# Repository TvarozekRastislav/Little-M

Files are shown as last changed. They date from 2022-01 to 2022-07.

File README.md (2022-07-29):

# **Little M.**
<div style="text-align:center">
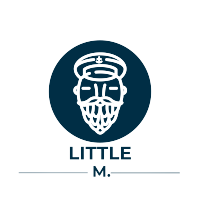
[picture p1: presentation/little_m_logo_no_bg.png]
    

Bechelors project of student at FEI STU Bratislava.<br> It is a prototype of little autonomous vehicle desinged to be able to orientate inside a building.<br>
Example video 1. - https://youtu.be/EsY_k1E6DLk<br>
Example video 2. - https://youtu.be/gij7saN3cls<br>
Bakalársky projekt študenta na FEI STU Bratislava.<br> Jedná sa o návrh malého autonómneho robotického vozdila s orientáciou v interieri.<br> Scrollni dole pre slovenský jazyk
</div>

---

## **Principle**
The basis of the project is the idea that there is already a wifi network almost everywhere around us. Using certain techniques, we can measure the Wi-Fi signal strength at a given location.
Determining which room the vehicle is in is based on collecting data on different signal strengths, different Wi-Fi networks (three in the project) and assigning the "id" of the room to these Wi-Fi networks. Subsequently, the data is processed and a model with an SVM calcifier is trained with them, so it is a so-called learning with a teacher. With the help of the openSource library, this model is subsequently converted into the C language so that it can be used in a vehicle that can use this model and the strength of the signal to find out which room it is in.

Project is composed from this parts
- ### data collector

- ### modeling part
- ### vehicle
---
### **data collector**
The purpose of this device is to measure signal strengths at the locations chosen by us.\
The preferred number is to perform 15 measurements in each room.\
The number of rooms is arbitrary.\
It consists of a USB Adapter for ESP-01, ESP8266 ESP-01 and a button that is used to access the programming mode.\
In the code, it is necessary to select the number of rooms, the number of Wi-Fi networks, their names, and how many measurements should be performed in each room.\
The code can be logged using putty or other software.\
When uploading the code, we will put the module into programming mode so that we hold the button while inserting it into the USB port.\
When programming, we must pay attention to the correct setting of the boaud height.\
**Parts**:
- Adapter for ESP-01
- ESP8266 ESP-01
- button

**schema**: 
- [schemas/zber_dat_png.png](https://github.com/TvarozekRastislav/Little-M./blob/main/schemas/zber_dat_png.png)

**code**:
- [code_base/data_collection.ino](https://github.com/TvarozekRastislav/Little-M./blob/main/code_base/data_collection/data_collection.ino)

**picture**:
- [hardware_pics/signal_collector.ino](https://github.com/TvarozekRastislav/Little-M./blob/main/hardware_pics/signal_collector.png)

---
### **Modeling part**

The task of the model part is to generate a "clean" csv file from the logged output from the previous part and use this file to train a model that uses the SVM classifier and then convert this model to a C file that can be used in Arduino using the open source micromlgen library.\
The model part can be done in two ways, by starting two jupyter notebooks or by setting the config and local execution of the script below or by pushing new input data.txt to the main branch, the GitHub action is started which generates the model and pushes it to GitHub.
With jupyternotebook, we can also see extra graphs related to data.

**schema**:
- [schemas/software_schema.png](https://github.com/TvarozekRastislav/Little-M./blob/main/schemas/software_schema.PNG)

**code**

***manual***:
- [code_base/data_clear_jupyter.ipynb](https://github.com/TvarozekRastislav/Little-M./blob/main/code_base/data_clear_jupyter.ipynb)
   - in the same folder, there must be an input file with data with the format from the previous section
   - the output is a csv file
- [code_base/data_train_model_jupyter.ipynb](https://github.com/TvarozekRastislav/Little-M./blob/main/code_base/data_train_model_jupyter.ipynb)
    - in the same folder, there must be an input file csv file with formatted data from the guessing point
    - the output is the model.h file which contains the trained model

***with help of script***:
- [code_base/create_model_automatic/config.json](https://github.com/TvarozekRastislav/Little-M./blob/main/code_base/create_model_automatic/config.json)
    - config needs to be changed to the required parameters
- [code_base/create_model_automatic/generate_model_from_data_file.py](https://github.com/TvarozekRastislav/Little-M./blob/main/code_base/create_model_automatic/generate_model_from_data_file.py)
    - to run the scirpt following requirements are required - [.github/workflows/requirements.txt](.github/workflows/requirements.txt)
---
### **Vehicle**
The vehicle uses an Arduino Uno and an Arduino sensor shield due to the large number of GND and VCC pins. The vehicle is powered by 4 motors that are controlled by H bridge modules, which allows you to set the speed of the vehicle as well as the direction of travel.\
  The Arduino is powered by two 4.5V batteries.
  It contains an ultrasonic sensor, a bluetooth receiver, ESP-01, a display that shows the current room in which the vehicle is located, 3 sensors for tracking a line on the ground.\
  The first code needs to be uploaded to the Arduino, the second to the ESP-01, then the vehicle can easily be controlled via a phone with a bluetooth connection, where the driving mode can be set, which will be line tracking or remote control.

 **schema**:
- [schemas/car_connected_pdf.png](https://github.com/TvarozekRastislav/Little-M./blob/main/schemas/car_connected_pdf.pdf)

**code**
- [code_base/car_code/main.ino](https://github.com/TvarozekRastislav/Little-M./blob/main/code_base/car_code/main/main.ino)
    - v rovnakom priečinku sa musí nachádzať aj model.h
    - tento kód je ptrebné nahrať na arduino
- [code_base/sending_via_rxtx](https://github.com/TvarozekRastislav/Little-M./blob/main/code_base/auto_wifi_signal_sender/sending_via_rxtx/sending_via_rxtx.ino)
    - tento kód je potrebné nahrať na ESp-01

**picture**:
- [hardware_pics/little_m_back.png](https://github.com/TvarozekRastislav/Little-M./blob/main/hardware_pics/little_m_back.png)

---

## **Princíp**
Základom projektu je myšlienka že takmer všade okolo nás sa už nachdáza wifi sieť. Pomocou určitých techník vieme zmerať silu wifi signálu na danom mieste.
Zisťovanie v akej miestnosti sa vozdilo nachádza je založené na zbere dát o rôznych silách signálov, rôznych wifi sietí(v projekte troch) a priradovania týmto wifi sietam aj "id" miestnosti. Následne sú dáta spracované a je nimi natrénovaný model s SVM kalsifikátorom teda ide o tzv. učenie s učiteľom. Pomocou openSource knižnice je následne tento model prevedený do jazyka C aby bol použiteľný vo vozidle ktoré vie pomocou tohoto modelu a sily signálu zistiť v akej miestnosti sa nachdáza.

Projekt je zložený z troch častí: 
- ### zariadenie na zber dát

- ### modelová časť
- ### vozidlo
---
### **Zariadenie na zber dát**
Toto zariadenie má za úlohu zmerať sily signálov na nami zvolených miestach.\
Preferovaný počet je v každej miestnosti vykonať 15 meraní.\
Počer miestností je ľubovoľný.\
Skladá sa z USB Adaptéra pre ESP-01, ESP8266 ESP-01 a tlačidla ktoré je používané na sprístupnenie programovancieho módu.\
V kóde je potrebné zvoliť počet miestností, počet wifi sietí, ich mená, a koľko meraní má byť v každej miestnosti vykonaných.\
Kód je možné loggovať pomocou putty alebo iného softwaru.\
Pri nahrávaní kódu uvedieme modul do programovacieho módu tak že pri vkladaní do USB portu budeme držať tlačidlo.\
Pri programovaní musíme dbať na správne nastavenie výšky boaudov.\
**súčiastky**:
- Adaptér pre ESP-01
- ESP8266 ESP-01
- tlačidlo

**schéma**: 
- [schemas/zber_dat_png.png](https://github.com/TvarozekRastislav/Little-M./blob/main/schemas/zber_dat_png.png)

**kód**:
- [code_base/data_collection.ino](https://github.com/TvarozekRastislav/Little-M./blob/main/code_base/data_collection/data_collection.ino)

**fotka**:
- [hardware_pics/signal_collector.ino](https://github.com/TvarozekRastislav/Little-M./blob/main/hardware_pics/signal_collector.png)

---
### **Modelová časť**

Modelová časť má za úlohu z loggovaného výstupu z predchádzajúcej časti vygenrovať "clean" csv súbor a pomocou tohoto súboru natrénovať model ktorý využíva SVM klasifikátor a následne tento model pomocou open source knižnice micromlgen prekonvertovať na súbor v jazyku C ktorý je možné využiť v arduine.\
Modelovú časť možno vykonať dvoma spôsobmi a to spustením dvoch jupyter notebookov alebo nastavením configu a lokálneho spustenia scriptu ktorý sa nachádza nižšie alebo pushnutím nových vstupných dát.txt do main branche sa spustá GitHub action  ktorá model vygeneruje a pushne na GitHub.
Pri jupyternotebooku môžeme vidieť aj extra grafy týkajúce sa dát.

**schéma**:
- [schemas/software_schema.png](https://github.com/TvarozekRastislav/Little-M./blob/main/schemas/software_schema.PNG)

**kód**

***manuálne***:
- [code_base/data_clear_jupyter.ipynb](https://github.com/TvarozekRastislav/Little-M./blob/main/code_base/data_clear_jupyter.ipynb)
    - v rovnakom priečinku sa musí nachádzať vstupný súbor s dátami s formátom z predchádzajúcej časti
    - vystupom je csv súbor 
- [code_base/data_train_model_jupyter.ipynb](https://github.com/TvarozekRastislav/Little-M./blob/main/code_base/data_train_model_jupyter.ipynb)
    - v rovnakom priečinku sa musí nachádzať vstupný súbor csv súbor s formátovanými dátami z predhádzajúceho bodu
    - výstupom je model.h súbor ktorý obsahuje natrénovaný model

***pomocou configu a scriptu***:
- [code_base/create_model_automatic/config.json](https://github.com/TvarozekRastislav/Little-M./blob/main/code_base/create_model_automatic/config.json)
    - config je potrebné zmeniť na požadované parametre
- [code_base/create_model_automatic/generate_model_from_data_file.py](https://github.com/TvarozekRastislav/Little-M./blob/main/code_base/create_model_automatic/generate_model_from_data_file.py)
    - na spustenie scriptu sú potrebné moduly ktoré sa nachádzajú v - [.github/workflows/requirements.txt](.github/workflows/requirements.txt)
---
### **Vozidlo**
Vozidlo využíva Arduino Uno a Arduino sensor shield kvoli veľkému množstvu GND a VCC pinov. Vozidlo je poháňané 4 motormi ktoré sú ovladané H bridge modulov, ktorý umožňuje nastavať rýchlosť vozidla ako aj smer jazdy.\
 Arduino je napájané dvomi 4.5V batériami.
 Obsahuje ultrazvukový senzor, bluetooth prijímač, ESP-01, display ktorý zobrazuje aktuálnu miestnosť v ktorej sa vozidlo nachádza, 3 senzori na sledovanie čiary na zemi.\
 Prvý kód je potrebné nahrať do Arduina druhý na ESP-01, potom je už jednoducho možné vozidlo ovládať cez telefón s bluetooth pripojením, kde sa dá nastavoať mód jazdy, a to bude sledovanie čiary alebo diaľkové ovládanie.

 **schéma**:
- [schemas/car_connected_pdf.png](https://github.com/TvarozekRastislav/Little-M./blob/main/schemas/car_connected_pdf.pdf)

**kód**
- [code_base/car_code/main.ino](https://github.com/TvarozekRastislav/Little-M./blob/main/code_base/car_code/main/main.ino)
    - v rovnakom priečinku sa musí nachádzať aj model.h
    - tento kód je ptrebné nahrať na arduino
- [code_base/sending_via_rxtx](https://github.com/TvarozekRastislav/Little-M./blob/main/code_base/auto_wifi_signal_sender/sending_via_rxtx/sending_via_rxtx.ino)
    - tento kód je potrebné nahrať na ESp-01

**fotka**:
- [hardware_pics/little_m_back.png](https://github.com/TvarozekRastislav/Little-M./blob/main/hardware_pics/little_m_back.png)

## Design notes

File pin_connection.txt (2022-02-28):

Servo - 9

H-bridge:
ENA - 3
ENB - 6
IN1 - 10
IN2 - 11
IN3 - 12
IN4 - 13 

Ultra Sensor:
trig - A1 
echo - A0

track-middle - 8
track-left - 7
track-right - 5

esp8266_module_rx - 2
esp8266_module_tx - 4

bluetooth_rx - tx 
bluetooth_tx - rx

Display: 
SDA - A4
SCL - A5

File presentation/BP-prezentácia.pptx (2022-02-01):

## AUTONÓMNE RIADENIE VOZIDLA V INTERIÉRI

Vedúci bakalárskej práce: Ing. Štefan (https://is.stuba.sk/auth/lide/clovek.pl)Bucz (https://is.stuba.sk/auth/lide/clovek.pl), PhD. (https://is.stuba.sk/auth/lide/clovek.pl)

Vypracoval: Rastislav Tvarožek

## OBSAH

1. Motivácia 2. Návrh riešenia 3. Hardware 4. Software 5. Plán na budúci semester

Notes: Abstrahovanie kvoli času

## MOTIVÁCIA

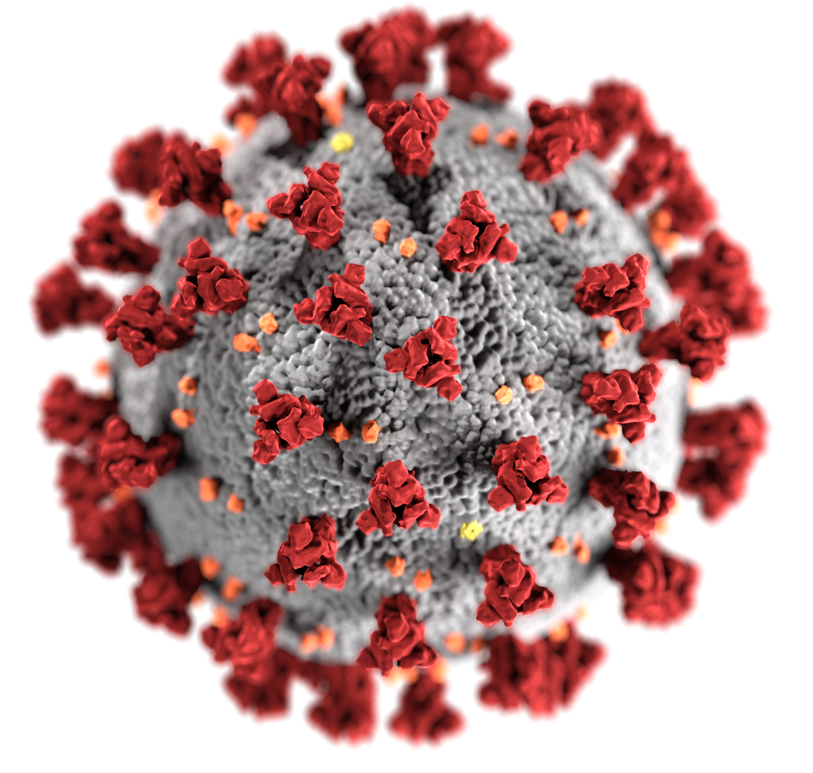
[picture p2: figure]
Obrázok, na ktorom je koláč, ozdobené, ovocie, pestrofarebné Automaticky generovaný popis

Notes: Výzva, novinka, dielna súčiastky, všetko je jednoduché , Medicína jeden chladiak jeden robo za sebou ambulancie ciary

## NÁVRH RIEŠENIA

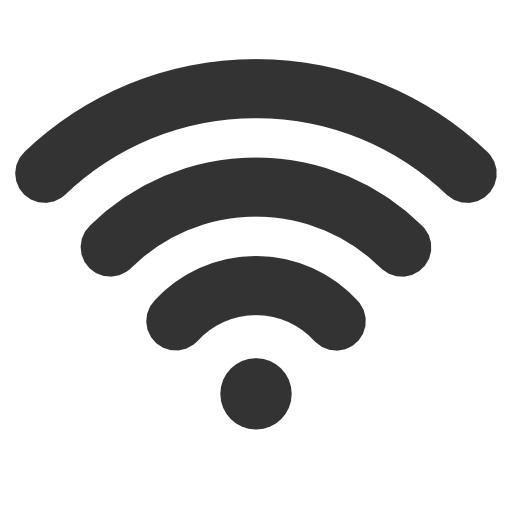
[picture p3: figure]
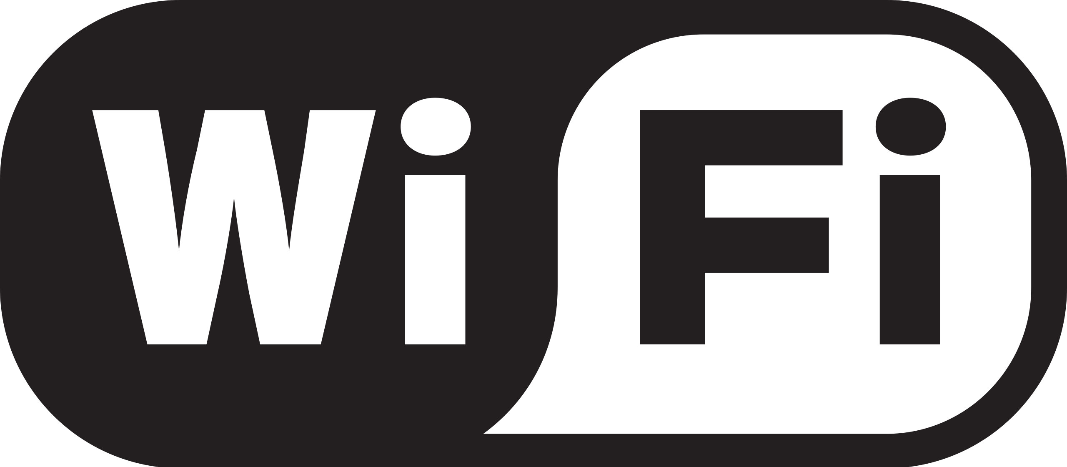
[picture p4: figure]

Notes: Niekolko wifi sietii

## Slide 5

HARDWARE

1. MODUL NA ZBER DÁT
2. VOZIDLO

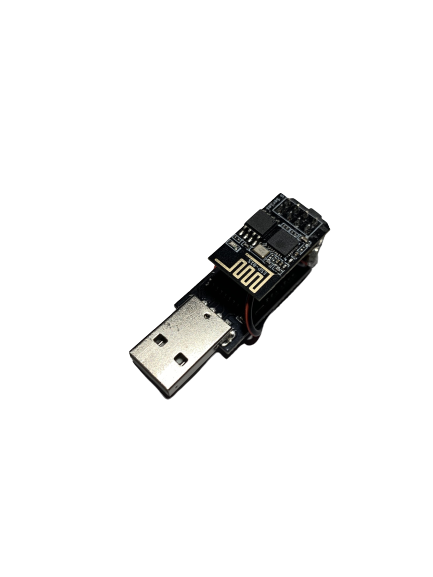
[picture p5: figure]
Obrázok, na ktorom je zapaľovač Automaticky generovaný popis

ESP8266 USB SERIAL PROGRAMMER

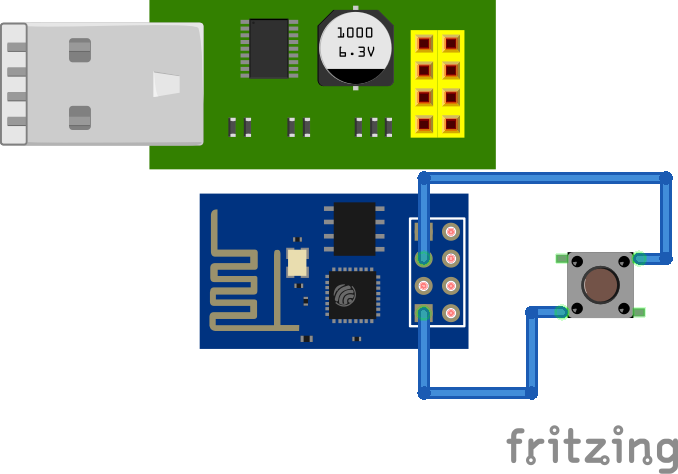
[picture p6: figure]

WIFI modul ESP-01 s ESP8266

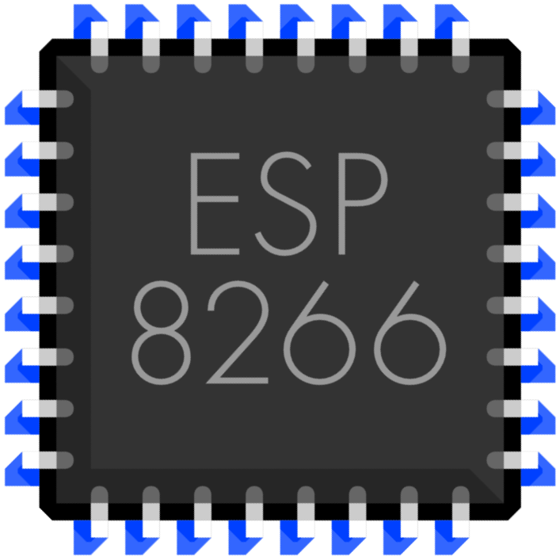
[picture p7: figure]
ESP8266 WiFi Project - DHT22 DeepSleep naar EmonCMS (logger)

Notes: Zbiera údaje ako až na dalšom slajde, otázky neváhajte ma zastaviť

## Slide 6

VOZIDLO

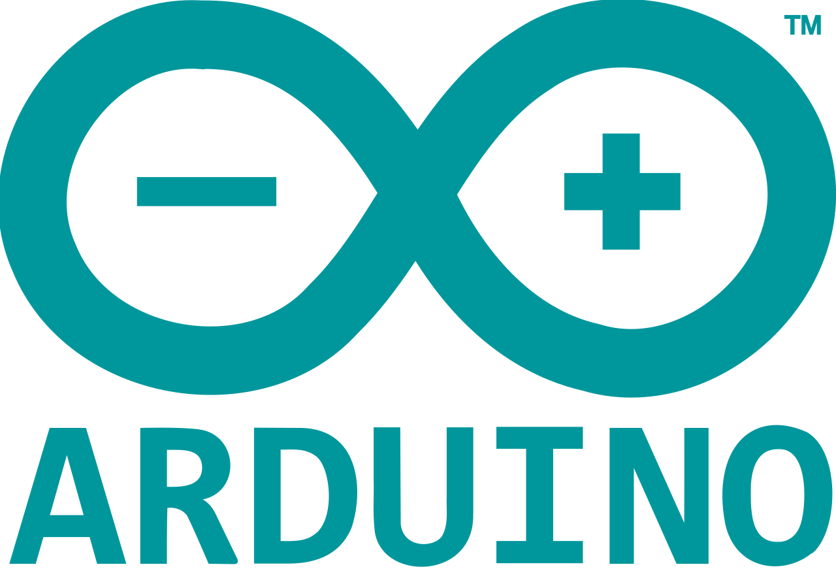
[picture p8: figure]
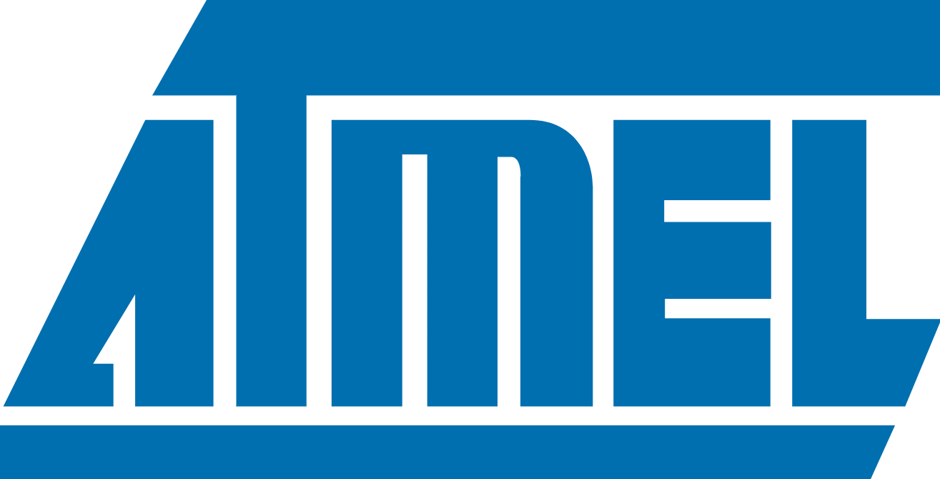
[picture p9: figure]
ATmega328 AU programmeren met Arduino als ISP
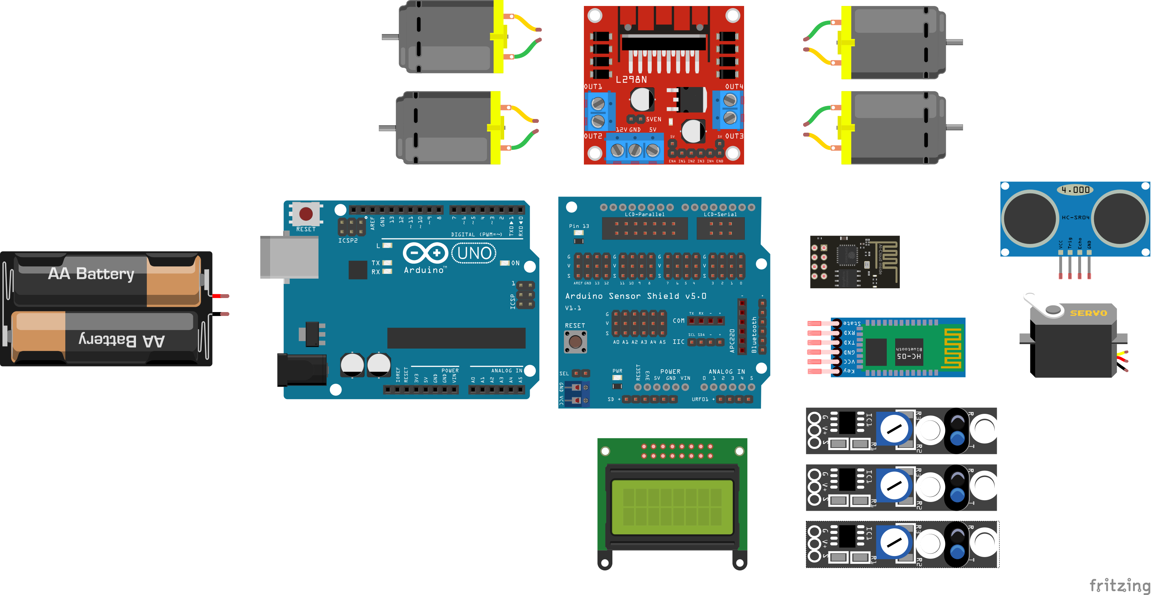
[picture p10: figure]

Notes: Popísať jednotilive prvky prečo nie siu zapojene

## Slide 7

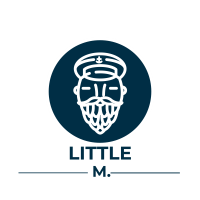
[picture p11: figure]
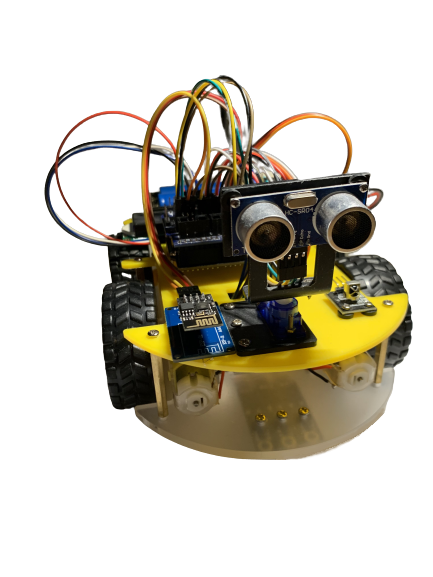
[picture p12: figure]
Obrázok, na ktorom je žltý Automaticky generovaný popis
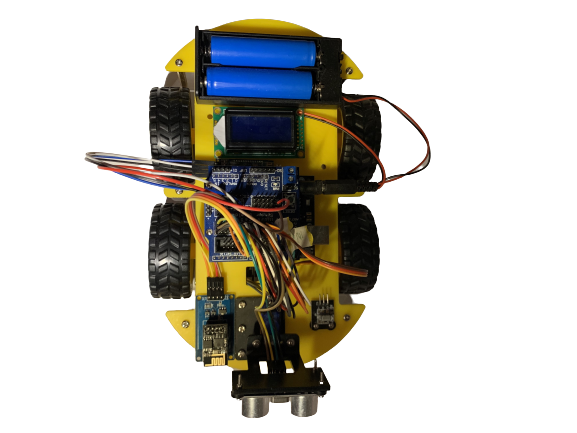
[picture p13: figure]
Obrázok, na ktorom je žltý, motor, automat Automaticky generovaný popis

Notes: Popisat fotografiu a logo

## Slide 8

SOFTWARE

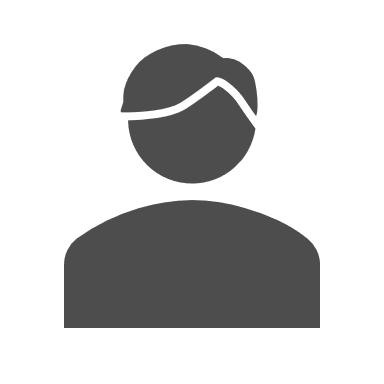
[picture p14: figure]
Mužský profil výplň plnou farbou
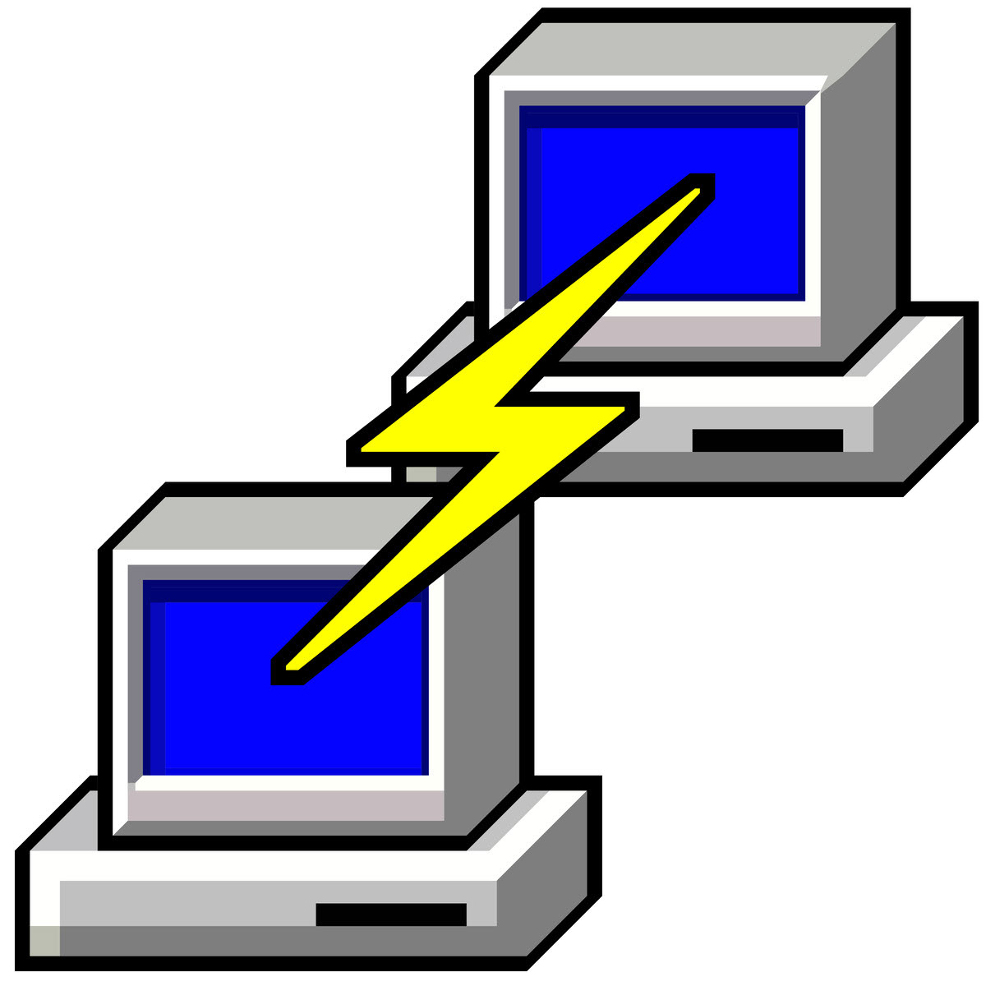
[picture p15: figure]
PuTTY svg logo on Behance
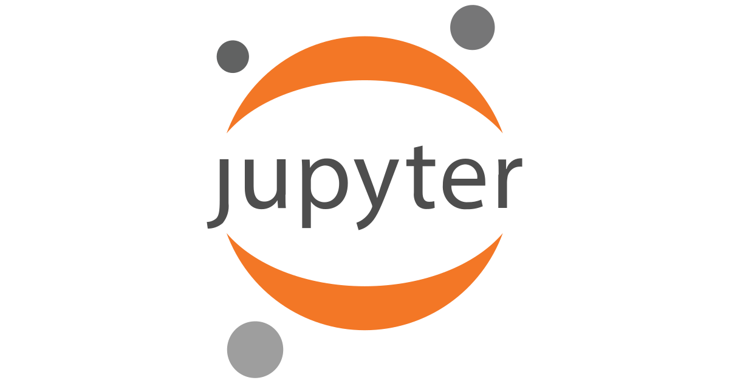
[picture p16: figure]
Project Jupyter | Home
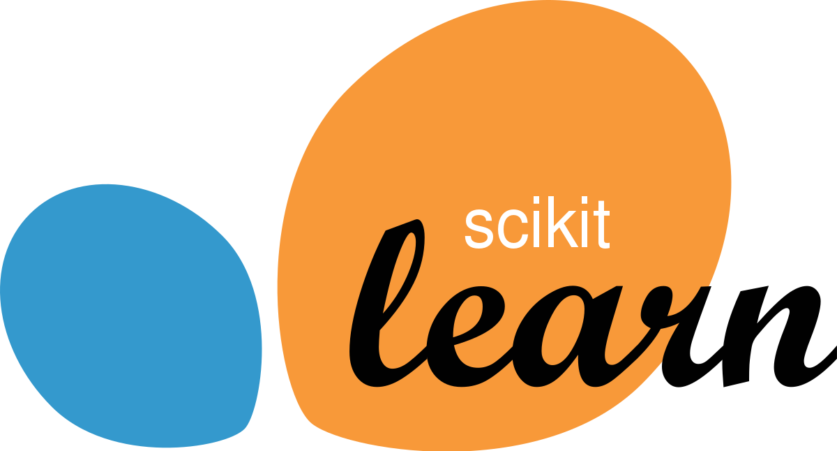
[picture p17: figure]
scikit-learn - Wikipedia
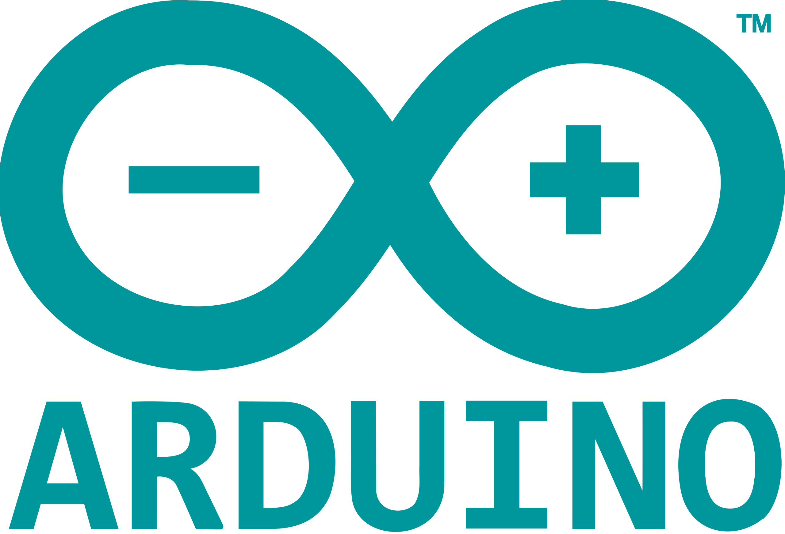
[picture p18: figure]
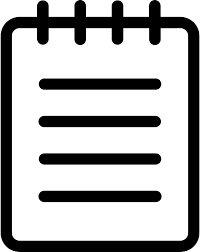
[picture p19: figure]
Notepad icon PNG and SVG Vector Free Download
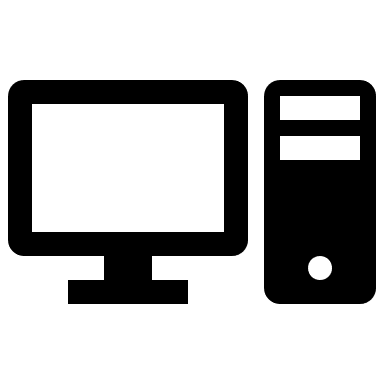
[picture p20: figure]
Počítač výplň plnou farbou
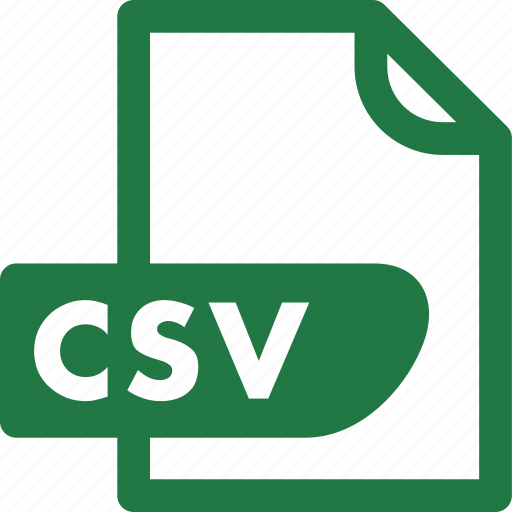
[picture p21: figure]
Csv, file, plano icon - Download on Iconfinder on Iconfinder

micromlgen

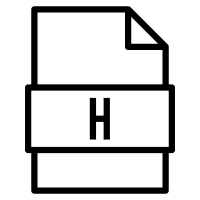
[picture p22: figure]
H File Icon - Download H File Icon 3001070 | Noun Project
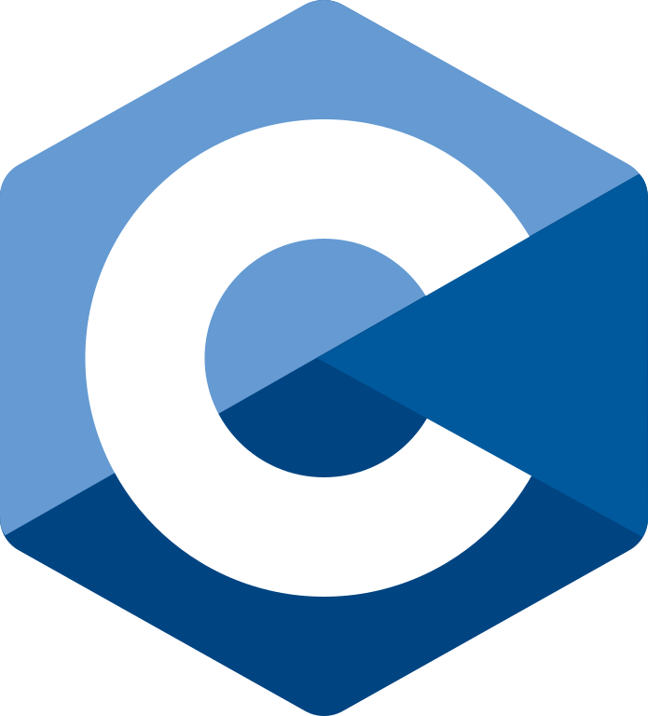
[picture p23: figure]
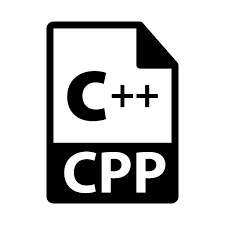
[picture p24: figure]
C++ Logo Download Icon PNG Transparent Background, Free Download #28398 - FreeIconsPNG
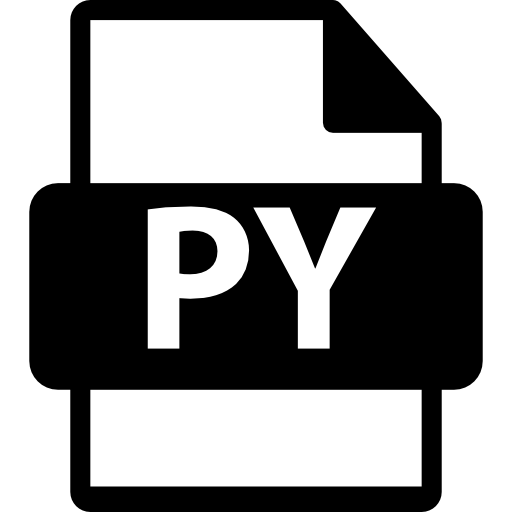
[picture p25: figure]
Free Icon | Py file format

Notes: Software popísať jednotlive subory. Nasa space x úspešnos swm

## PLÁN NA BUDÚCI SEMESTER

- Napísať bakalársku prácu
- Pripojiť display
- Predný senzor program
- Upraviť kód(„multithreading (Protothreading)“,automatické spúšťanie skriptov)
- Optimalizácia modelu
- Optimalizácia kódu
- Vizuálna úprava kabeláže
- Otestovanie funkčnosti
- Grafické znázornenie SVM

## ĎAKUJEM ZA POZORNOSŤ

https://github.com/TvarozekRastislav/Little-Misko

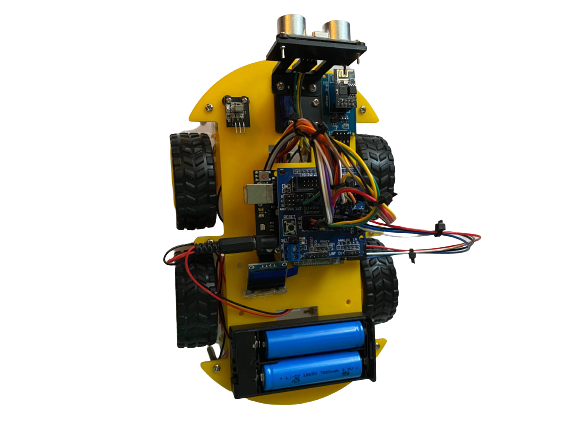
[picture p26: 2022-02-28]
hardware_pics/little_m_back.png

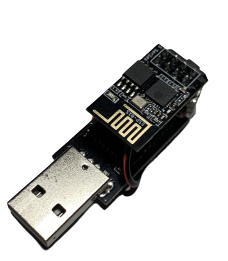
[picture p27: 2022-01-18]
hardware_pics/signal_collector.png

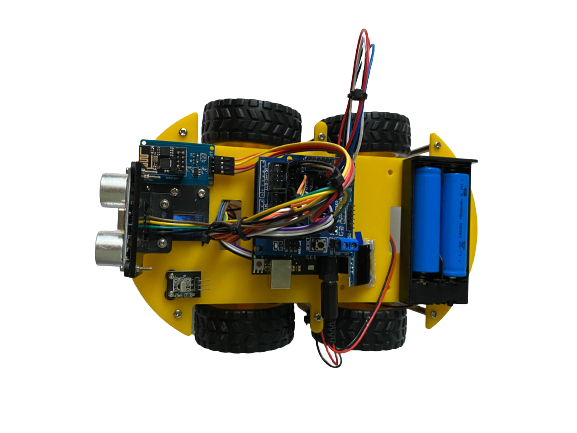
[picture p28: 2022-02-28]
hardware_pics/little_m_side.png

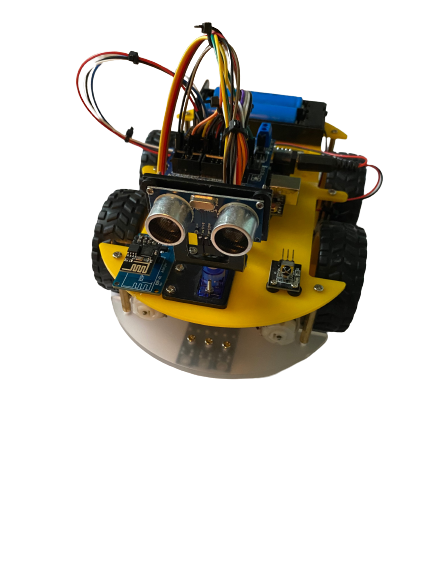
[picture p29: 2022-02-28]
hardware_pics/little_m_front.png

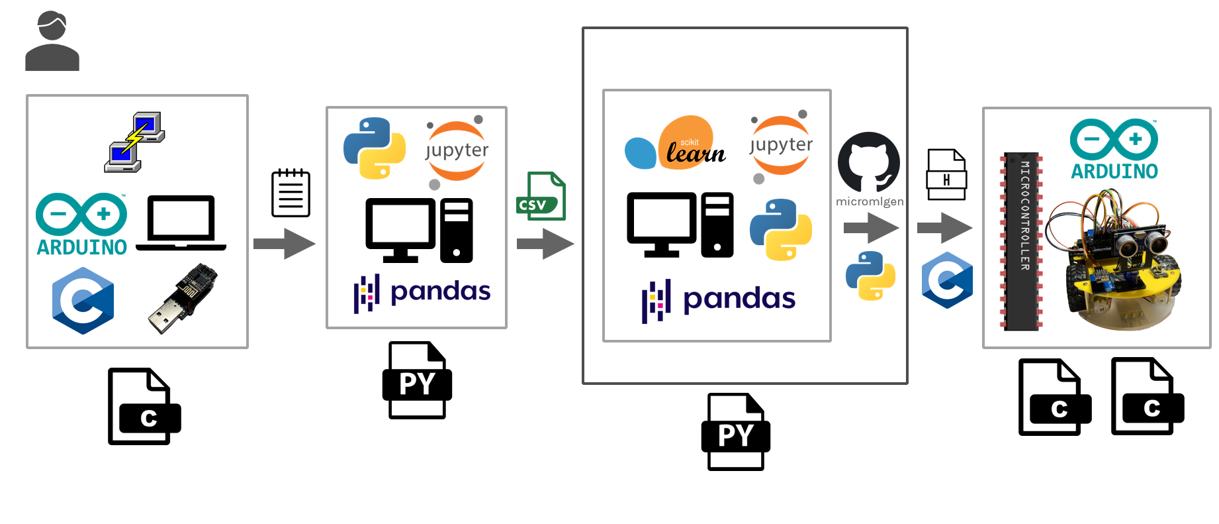
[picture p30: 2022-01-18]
schemas/software_schema.PNG

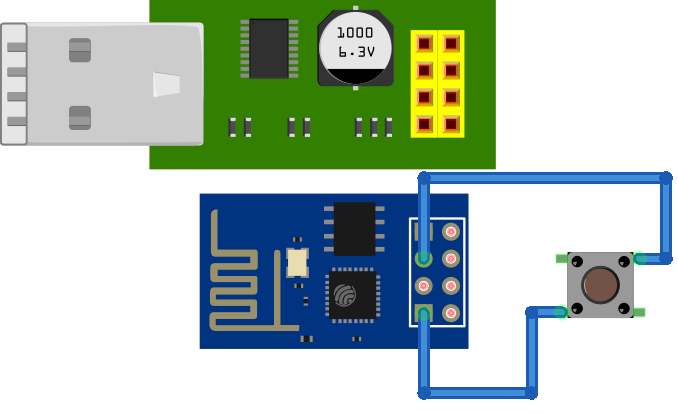
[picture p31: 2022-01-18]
presentation/zber_dat_png.png

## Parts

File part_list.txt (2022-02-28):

Zariadenie na zber dát:

Adaptér pre ESP-01
ESP8266 ESP-01
tlačidlo

Vozidlo: 
Arduino UNO R3
L298N
M2 * 4
Ultrazvukový senzor HC-SRO4
ESP8266 ESP-01
servo
2*4.5V batéria
OLED 0.96″ display 128×64
IIC Senzorový shield V5.0
bluetooth modul HC-05
batériový box
esp-01 adaptér 5V5
potenciometer

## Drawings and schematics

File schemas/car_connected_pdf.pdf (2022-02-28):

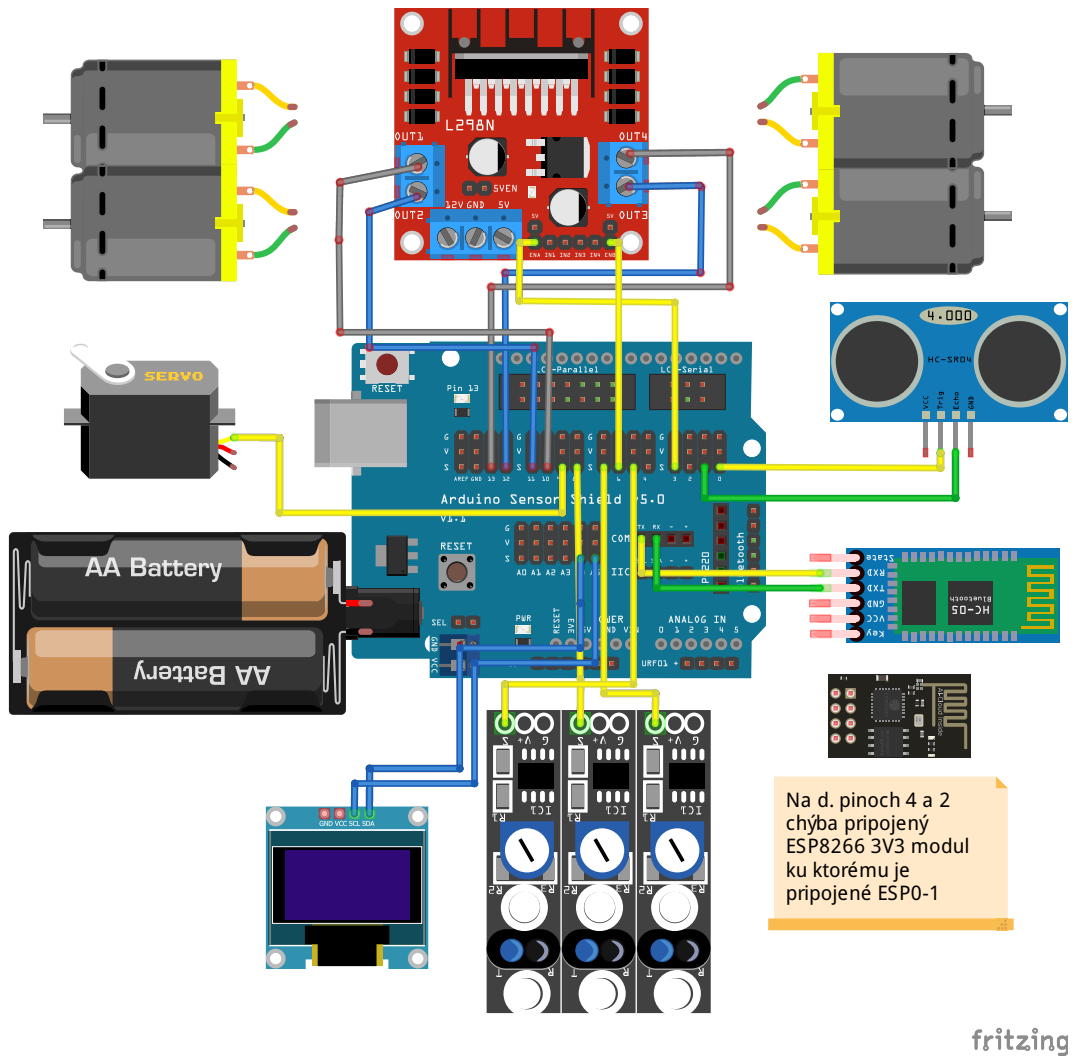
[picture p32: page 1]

Na d. pinoch 4 a 2
chýba pripojený
ESP8266 3V3 modul
ku ktorému je
pripojené ESP0-1

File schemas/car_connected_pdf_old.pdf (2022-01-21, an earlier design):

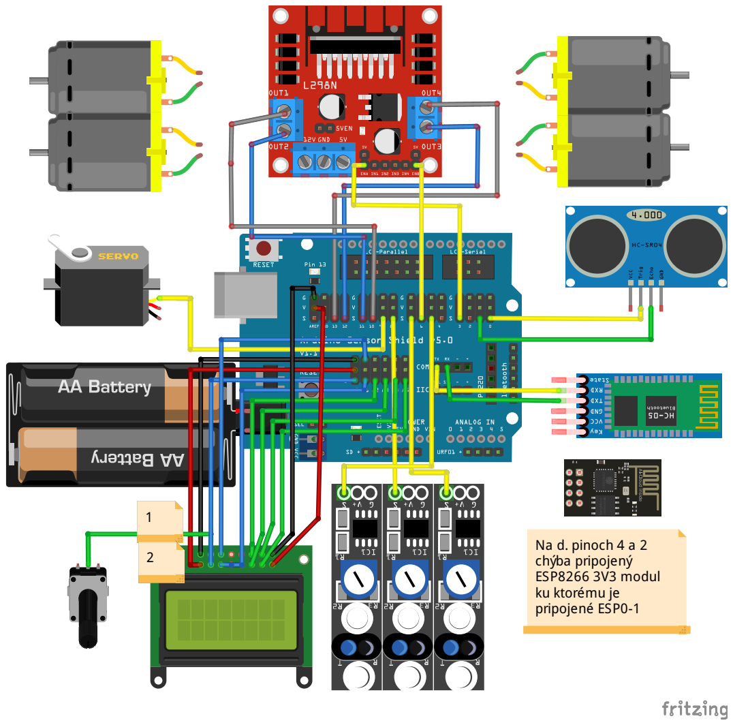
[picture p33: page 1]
d. pin o; rip; ul ku ktorému je pripojené ESP0-1

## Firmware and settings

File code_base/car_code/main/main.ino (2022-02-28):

#include <Adafruit_SSD1306.h>
#include <SoftwareSerial.h>
#include <Wire.h>
#include "model.h"

//module.c
Eloquent::ML::Port::SVM SVM_classifier;

//display
#define OLED_RESET -1 
#define SCREEN_ADDRESS 0x3C
#define SCREEN_WIDTH 128 
#define SCREEN_HEIGHT 32

//ESP comunication
#define rxPinEsp 4
#define txPinESp 2
//line sensors

#define sensor_left 7
#define sensor_middle 8
#define sensor_right 5
//ultrasound sensor

#define trigPin A1
#define echoPin A0

Adafruit_SSD1306 display(SCREEN_WIDTH, SCREEN_HEIGHT, &Wire, OLED_RESET);

//comunication with ESP
SoftwareSerial SerialEsp = SoftwareSerial(rxPinEsp, txPinESp);

//waiting for response multitasking
unsigned long esp_read_interval = 1000;
unsigned long time_for_action = 0;

//motor pins
const int IN_1 = 10;
const int IN_2 = 11;
const int IN_3 = 12;
const int IN_4 = 13;
const int EN_A = 3;
const int EN_B = 6;

//beginning mode, default speed and bluetooth variable
int mode_maunal = 0;
char Incoming_value = 0;
int speed = 60;

//room deciding
int first_signal = 0;
int second_signal = 0; 
int third_signal = 0;

//line following sensors
unsigned char state_left;
unsigned char state_middle;
unsigned char state_right;


//room decision
short room = 0;
short prev_predict = 0;

//sending and recieving from ESP
int s_sent = 0;
short counter = 0;

//front sensor
long duration; 
long distance;


void motor_control_IO_config(){
  pinMode(IN_1, OUTPUT);
  pinMode(IN_2, OUTPUT);
  pinMode(IN_3, OUTPUT);
  pinMode(IN_4, OUTPUT);
  pinMode(EN_A, OUTPUT);
  pinMode(EN_B, OUTPUT);
}

void stop(){
  analogWrite(EN_A, 0);
  analogWrite(EN_B, 0);
}

void ride(uint8_t in_1,uint8_t in_2, uint8_t in_3, uint8_t in_4, int en_A, int en_B ){

  digitalWrite(IN_1, in_1);
  digitalWrite(IN_2, in_2);

  digitalWrite(IN_3, in_3);
  digitalWrite(IN_4, in_4);

  analogWrite(EN_A, en_A);
  analogWrite(EN_B, en_B );
}

void sensor_IO_config(){
  pinMode(sensor_left, INPUT);
  pinMode(sensor_right, INPUT);
  pinMode(sensor_middle, INPUT);
}

void read_room(){
  
  if(s_sent == 0){
    SerialEsp.write('s');
    s_sent = 1;
  }

  if(millis() > time_for_action){
      time_for_action = millis() + esp_read_interval;
      Serial.println(SerialEsp.available());
      if(SerialEsp.available()==3){
        s_sent = 0;
        Serial.println("prisli bajty");
        Serial.println(SerialEsp.available());
        first_signal = SerialEsp.read()* (-1);
        second_signal = SerialEsp.read()* (-1);
        third_signal = SerialEsp.read() * (-1);
        
        Serial.println(first_signal);
        Serial.println(second_signal);
        Serial.println(third_signal);

        counter = 0;
        get_room();
      }
      else{
        Serial.println("prislo menej bajtov!");
        counter++;
        while(SerialEsp.available() > 0){
         char t = SerialEsp.read();
      }
      if(counter == 5 ){
        SerialEsp.write('s');
        counter= 0; 
        Serial.write("poslal som s");
      }
      first_signal = 0;
      second_signal = 0;
      third_signal = 0;
      return;
      }
   }
}

void get_room(){
  
  if(first_signal == 0 || second_signal == 0 || third_signal == 0){
    Serial.println("prislo malo signalov");
    return;
  }
  
  if(first_signal == 1 || second_signal == 1 || third_signal == 1){
    Serial.println("prislo poskodeny signal");
    return;
  }
  
  float features[] = {first_signal, second_signal, third_signal};
  String output_str = SVM_classifier.predictLabel(features);
  int output = output_str.toInt();
  
  Serial.println("------------------");
  Serial.println("konkretna miestnost:");
  Serial.println(output);
  Serial.println("predchadazaujca miestnost:");
  Serial.println(prev_predict);
  
  if(prev_predict == output){
    room = output;
  }
    
  Serial.println("daná miestnost:");
  
  display.clearDisplay();
  display.setCursor(0,0);
  display.setTextSize(2);           
  display.setTextColor(SSD1306_WHITE);
  display.println(("ROOM:"));
  display.println(room);
  display.display();
  
  Serial.println(room);
  Serial.println("------------------");
  prev_predict = output;
}

void tracking_scan(){
  state_left = digitalRead(sensor_left);
  state_middle = digitalRead(sensor_middle);
  state_right = digitalRead(sensor_right);
}  

void calcDistance(){
  digitalWrite(trigPin, LOW);
  delayMicroseconds(2);
  digitalWrite(trigPin, HIGH);
  delayMicroseconds(10);
  digitalWrite(trigPin, LOW);
  duration = pulseIn(echoPin, HIGH);
  distance = duration * 0.034 / 2; 
  }
  
void setup(){ 
  //display setup
  display.begin(SSD1306_SWITCHCAPVCC, SCREEN_ADDRESS);
  display.clearDisplay();
  display.display();
  display.setTextSize(2);            
  display.setTextColor(SSD1306_WHITE);       
  display.setCursor(0,0);             
  display.println(F("ROOM:"));
  display.display();
  
  //com with ESP
  pinMode(rxPinEsp, INPUT);
  pinMode(txPinESp, OUTPUT);
  //sensor setup
  pinMode(trigPin, OUTPUT); 
  pinMode(echoPin, INPUT); 
  //com setup
  Serial.begin(9600); 
  SerialEsp.begin(115200);
  //motor setup
  motor_control_IO_config();
  //line sensors setup
  sensor_IO_config();
}



void loop(){
  
  if (Serial.available() > 0){
    Incoming_value = Serial.read();
    Serial.print(Incoming_value);  
    Serial.print("\n");
    
    if (Incoming_value == 'c'){
      mode_maunal = 1;
    }
    else if (Incoming_value == 'C'){
      mode_maunal = 0;
    }
    
    if (mode_maunal == 1){
      if (Incoming_value == '1'){
        Serial.print("idzeeeeeeem j ");
        ride(LOW, HIGH, HIGH, LOW ,speed, speed+10); //forward
      }
      else if (Incoming_value == '2'){
        ride(LOW, HIGH, HIGH, LOW ,0, 120); //right
      }
      else if (Incoming_value == '3'){
        ride(HIGH, LOW, LOW, HIGH ,speed, speed+10); //back 
      }
      else if (Incoming_value == '4'){
        ride(LOW, HIGH, HIGH, LOW ,100, 0); //left    
      }
      else{
      stop();
      }
    }
  read_room();
  }
  
  if (mode_maunal == 0){
    read_room(); 
    tracking_scan();
      
    if (state_middle == HIGH){
      if (state_left == LOW & state_right == HIGH){
        ride(LOW, HIGH, HIGH, LOW ,0, 120); //right
      }
      else if (state_right == LOW & state_left == HIGH){
        ride(LOW, HIGH, HIGH, LOW ,100, 0); //left    
      }
      else{
        ride(LOW, HIGH, HIGH, LOW ,speed, speed+10); //forward
      }
    }
    else{
      if (state_left == LOW & state_right == HIGH){
        ride(LOW, HIGH, HIGH, LOW ,0, 120); //right
      }
      else if (state_right == LOW & state_left == HIGH){
        ride(LOW, HIGH, HIGH, LOW ,100, 0); //left 
      }
      else{
        ride(HIGH, LOW, LOW, HIGH ,speed, speed+10); //back 
        delay(100);
        stop();
      }
    }
  }
  
  do{
    calcDistance();
  if(distance < 10){
    stop();
    }
  }
  while(distance <10);
}

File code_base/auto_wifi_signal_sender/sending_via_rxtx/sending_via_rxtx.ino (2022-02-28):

#include <ESP8266WiFi.h>

//------------set-up---------------
char wifi_ap_1[] = "rododendron";
char wifi_ap_2[] = "TP-LINK_9FE2A0";
char wifi_ap_3[] = "Router_3";
//---------------------------------

int numNetworks;

void setup(){
    Serial.begin(115200);
}

void loop(){
 if(Serial.available()){
    if(Serial.read() == 's'){
      numNetworks = WiFi.scanNetworks();
       for (int i = 0; i < numNetworks; i++){
        if (WiFi.SSID(i) == wifi_ap_1){   
          Serial.write(WiFi.RSSI(i)*(-1)); 
        }
        else if (WiFi.SSID(i) == wifi_ap_2){
          Serial.write(WiFi.RSSI(i)*(-1));
        }
        else if (WiFi.SSID(i) == wifi_ap_3){
          Serial.write(WiFi.RSSI(i)*(-1));
        }
      }
    }  
  }
}

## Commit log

2022-01-12 fix: code improvements/ car_code notworking
    [main.ino, sending_via_rxtx.ino]
2022-01-16 perf: trained model with 15 data, struct repo update
    [data_out.csv, data_out_1_10.csv]
2022-01-18 feat:code change car prepared for new model
    [car.fzz, zber_dat.fzz]
2022-01-18 docs: readme.md
    [car_connected.fzz]
2022-01-18 docs: some little changes
    [zber_dat.fzz]
2022-01-18 added pic
    [data_out.csv]
2022-01-18 docs: photo deletion
    [data_out_1_10.csv]
2022-01-19 feat: iplemented auto model.h file creation
    [data_out.csv]
2022-01-20 fix: car code
    [car_connected.fzz]
2022-01-21 docs: added display
    [car_connected.fzz, zber_dat.fzz]
2022-02-01 feat: 30p model working best, car_code change
    [data_out.csv, data_out_15.csv, data_out_15v2.csv]
2022-02-02 fix: loading txt file fixed
    [data_out.csv]
2022-02-02 feat: Updating the mode.h file
    [data_out.csv]
2022-02-15 feat: schema display update
    [car_connected.fzz]
2022-02-15 feat: front sensor implemented
2022-02-28 feat: new router implemented/gut working model
    [data_out.csv]
